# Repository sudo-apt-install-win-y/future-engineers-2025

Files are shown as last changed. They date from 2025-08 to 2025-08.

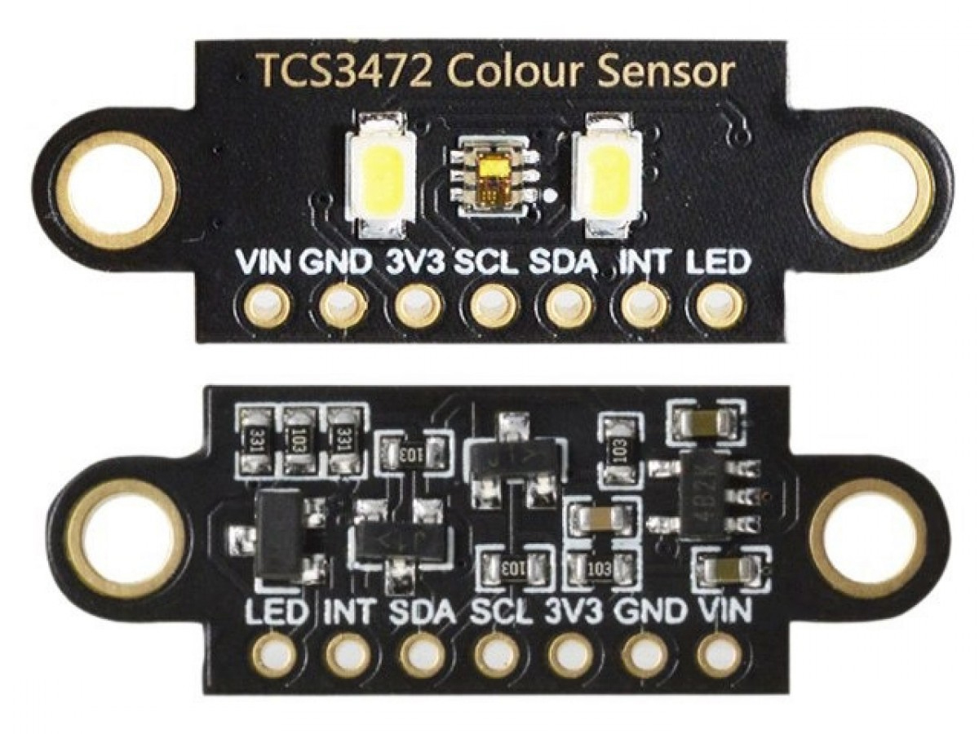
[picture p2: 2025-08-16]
docs/images/component_photos/TCS34725.jpg

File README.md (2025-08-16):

# sudo apt install win -y - WRO 2025 Future Engineers
**Category:** Future Engineers - Self-Driving Cars

**Team:** DJ_Theron, TheGuyInTheRedSuit

**Coach:** Jarret Williams

**Country:** South Africa

## Table of contents
### [Mobility Management](/docs/mobility-manegement.md)
### [Power and Sense Management](/docs/power-and-sense.md)
### [Obstacle Management](/docs/obstacle-management.md)
### [Pictures](/docs/images/)
### [Performance Videos](/videos/demo-vids.md)
### [3D Models](/hardware/3d_models/)
### [Source Code](/software/src/)
### [How to build the robot](/hardware/howtobuild.md)
### [How to setup the robot to run code](/software/setup.md)
### [BOM (Bill Of Materials)](/hardware/bom/bill-of-materials.csv)
### [Schematics](/hardware/schematics/)

---

## Hardware Overview
At the heart of our robot is a central processor that runs all operations, a [Raspberry Pi 4B 2GB](/docs/images/component_photos/RaspberryPi4B.jpg). Our robot features a Rear wheel drive and front wheel steering system (Ackermann), enabling easy turning and motion. Rubber tires are utilised for the grip they provide. The chassis's RWD function, explained earlier, is powered by a single 12V DC brushed motor. Steering functionality is provided by a 12V servo motor connected. 
( _An in depth mobility manegement document can be found [here](/docs/mobility-manegement.md)_ )
The robot uses four time-of-flight sensors ([VL53l0x](/docs/images/component_photos/vl53l0x.jpg)), one colour sensor ([tcs34725](/docs/images/component_photos/TCS34725.jpg)), one gyroscope and one Raspberry Pi Camera v3 to achieve sensor fusion and computer vision. The Pi is powered by a Waveshare UPS HAT B, which contains 2 18650 batteries. 3 18650 Batteries power the motors. Everything connects to a central ground. ( _An in-depth power and sensing document can be found [here](/docs/power-and-sense.md)_ )

## Software Architecture
We used Python to code our robot. The code consists of 3 main modules. round1.py handles the entirety of the Open Challenge (what we call Round 1). round1.py utilises the data gathered from the distance sensors, and it then uses a PID controller to keep itself between the walls of the course. round1.py also uses the colour sensor to detect the lines on the ground, which tell the robot when to turn. round2.py handles the entirety of the Obstacle Challenge (we call it Round 2). By using OpenCV contour and colour detection on live images captured from the camera, we can distinguish where and what colour the block in front of the robot is, and so the robot will steer the appropriate way around it. The code also checks for a purple item in the background, indicating a purple block. After seeing the purple block three times, it proceeds to parallel park between the purple blocks. button_watcher.py handles starting and stopping the programs and indicating what is happening using an led. It is run as a systemd service and it starts when the Pi powers on and listens for button presses. When the button is pressed after powering on it goes into "armed" mode which allows for a singular press to start the round1.py program and a long press to start the round2.py program. Once in a program the button can be pressed to stop the running program in case something goes wrong. All of our code is in Python (except the installer script which is written in bash). We used OpenCV for computer vision and a custom PID controller for sensor fusion.

## Hardware-Software Integration
There are 8 sensors on the robot we use to determine the 2 outputs that the robot has. There are 6 i2c sensor of which 4 are the Time of Flights, 1 is the colour sensor and the other is the  Gyroscipe. The time of flights connects to the raspberry pi using i2c adresses and provides distance data to round1.py. The colour sensor connects to the raspberry pi using i2c and provides RGB values to both round1.py and round2.py. The time of flights have xshut pins (connected to each their own GPIO) which are used to assign different i2c adresses to each and since the colour sensor doesnt have one we had to design one ourselves, using a transistor, also connected to a GPIO pin. The Gyroscope connects to the Raspberry Pi via i2c and provides yaw angle data to round1.py.

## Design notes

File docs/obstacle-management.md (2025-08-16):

# Round 1 Obstacles Management

In order to make our way around the track 3 times there were a few obstacles to overcome

## Knowing when to take a corner

Our robot looks at the lines on the ground and takes note of the colour. The line will be blue when we need to turn right and orange when we need to turn left. Once it detects the lines it will run a hardcoded cornering script to allow it to take the corner perfectly. l

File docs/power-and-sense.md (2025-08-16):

## Power and Sense Management
### Power
We use 3 18650 batteries to provide 10.8 - 11.1 volts to our motor driver board. The motor driver board powers our DC Motor and Servo. To power our Raspberry Pi 4 B we have 2 more 18650 Batteries in a Waveshare UPS Hat B. This provides a stable power source to our Pi at 7.2 - 7.4 volts directly onto the Pi's power rails through Pogo Pins.

### Time of Flight Sensors
Our robot has 4 VL53L0X Time of Flight sensors situated with 2 on either side of our robot to give us the distances between the walls and our robot. Using these, we also determine a rough angle of our robot by looking at the distances at the front and the back of our robot.

Instead of these Time of Flights, we would have preferred a lidar to detect the walls, maybe next year.

### Camera
The robot is also equipped with a Raspberry Pi Camera 3 Regular Angle (76 degrees) to see the red and green obstacles in round 2. 

### Direction Sensing
Our robot has a Gyroscope and accelerometer sensor (MPU60-50). We do not use the Accelerometer; we just use the Gyroscope to determine the angle of the robot. 

### Color sensing
Finally, we have a colour sensor to detect the orange and blue lines on the mat to know when to take the corner.

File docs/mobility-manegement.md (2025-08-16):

## Mobility Management
### Drivetrain type
Our robot is built like a normal RWD (Rear Wheel Drive) car you find in everyday life. This means it has two wheels at the rear of the robot, which provide drive. At the front of the robot, two wheels provide steering functionality. 
### Rear Drive Assembly
The rear axle is powered by a single 12V DC motor with external gears, which speeds the robot up to allow for faster driving around the board. These gears connect to a simple but reliable rear axle, which is held in place by two ball bearings on either side of the robot. These connect to two thick and grippy rubber wheels that provide strong traction to the board mat.
### Front Drive Assembly
The front wheels are not powered to provide traction but are used for steering to navigate obstacles, turn corners, and parallel park the robot. We used a standard 12V 180-degree servo motor to turn a certain amount or continue straight. The steering rack utilises Ackermann steering geometry to make sure that turns are taken properly, accounting for wheels on the inside and outside of a turn needing to trace out circles of different radii (since the inner wheel takes a tighter path while the outer wheel takes a wider path).

Ackermann Steering

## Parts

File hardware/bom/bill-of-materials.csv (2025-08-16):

Component | Description | Qty | Manufacturer | Purpose | Team_Fabricated | Source
Raspberry Pi 4B | Main computer 2GB RAM | 1 | RPi Foundation | Processing and vision | No | pishop.co.za
Pi Camera v3 | 8MP camera module | 1 | RPi Foundation | Track and object detection | No | pishop.co.za
DC Motor | 12V motor | 1 | Generic | Drive system | No | Hobby shop
Servo Motor | 180° standard servo | 1 | Generic | Steering control | No | Hobby shop
ToF Sensors | HC-SR04 distance sensors | 4 | Generic | Obstacle detection | No | Online supplier
Robot Chassis | Main frame structure | 1 | Custom | Mechanical support | No | Laser cut acrylic
Camera Mount | Camera holder | 1 | Custom | Vision system mount | Yes | 3D printed
Motor Driver | L298N dual H-bridge | 1 | Generic | Motor control | No | Electronics store
Custom PCB | Power distribution board | 1 | Custom | Wiring organization | Yes | Team designed
Battery | 7.4V Li-Po 1500mAh | 1 | Generic | Power supply | No | RC hobby store
Wheels | Rubber wheels 65mm | 4 | Generic | Movement and steering | No | Various suppliers
Hardware | Screws nuts spacers | Set | Generic | Assembly | No | Hardware store
Wiring | Jumper wires connectors | Set | Generic | Connections | No | Electronics store

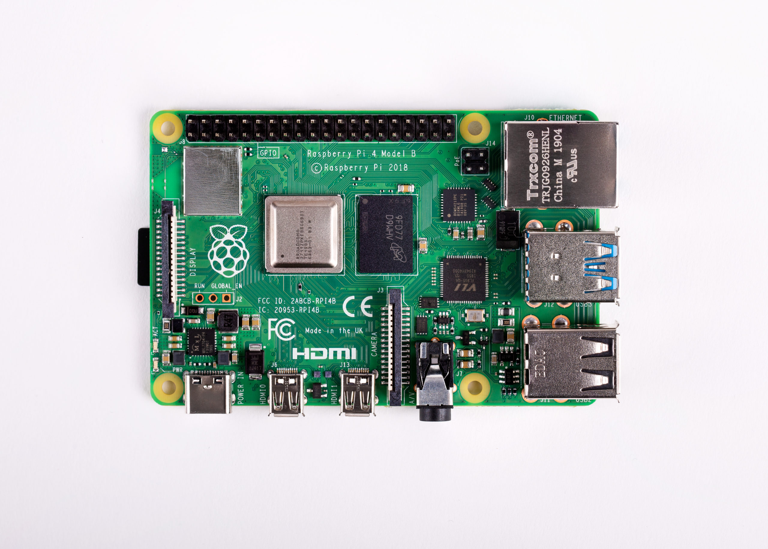
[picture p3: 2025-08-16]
docs/images/component_photos/RaspberryPi4B.jpg

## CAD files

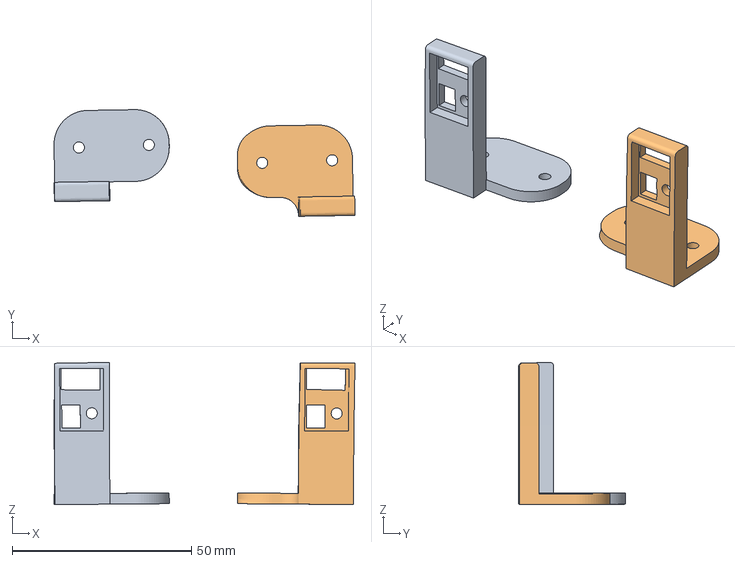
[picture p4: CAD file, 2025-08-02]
hardware/3d_models/ToF_Mount_Both.3mf
83.9 x 29.7 x 39.6 mm
ToFNicerLooking_Right.stl
ToFNicerLooking_Left.stl

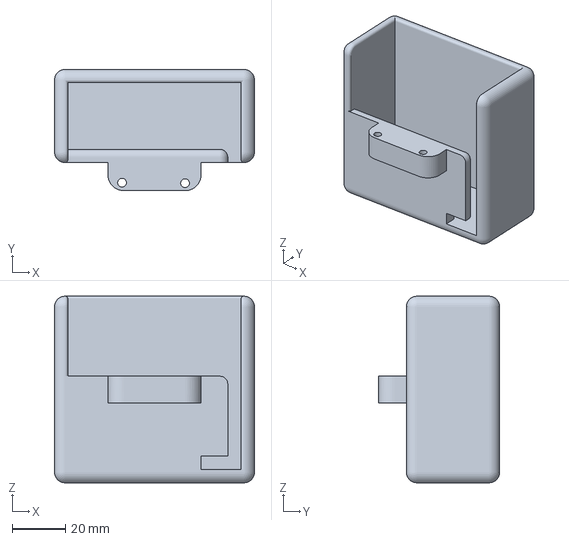
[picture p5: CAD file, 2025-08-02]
hardware/3d_models/Battery_Holder.3mf
75.0 x 45.5 x 70.0 mm

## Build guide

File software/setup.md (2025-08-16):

# How to setup the robot for code
Firstly you need to complete building the robot [here](/hardware/howtobuild.md)
## 1. Flash the SD Card
To get started you will need to flash the micro SD card that will be inserted into the Raspberry Pi
First go to [the raspberry pi downloads page](https://www.raspberrypi.com/software/) and download raspberry pi imager for your OS.
Then install the imager.
Open it. Insert the micro SD Card into your computer. Choose your model of pi on the app. choose full desktop environment. choose the microsd card. click flash. 

## 2. Setup the Pi
plug the microsd into your pi. turn it on. set up the pi by following the onscreen instructions. access the pi's terminal using ssh or a monitor and keybaord.

## 2. Run setup.sh
First you need to get the setup.sh code from its public github.
<pre>curl https://github.com/sudo-apt-install-win-y/setup-script/blob/main/setup.sh</pre>
Now you need to just run the bash file and everything should install.
<pre>bash setup.sh</pre>

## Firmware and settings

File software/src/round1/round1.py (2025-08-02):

import RPi.GPIO as GPIO
import time
import board
import busio
import digitalio
import adafruit_vl53l0x
import adafruit_tcs34725

IN1 = 17
IN2 = 27
ENA = 18
servo = 12

csensor = 0

Kp = 9
Ki = 0
Kd = 4

error = 0
current_time = 0
integral = 1
last_time = time.time()
dt = 0
steering_angle = 90
output = 0
last_error = 1

sensor1 = None
sensor2 = None
sensor3 = None
sensor4 = None

distance1 = 0
distance2 = 0
distance3 = 0
distance4 = 0

sensor_addresses = [0x30, 0x31, 0x32, 0x33]
sensor_shutdown_pins = [board.D5, board.D6, board.D13, board.D26]
sensors = []

turningright = False
turningleft = False


GPIO.setwarnings(False)
GPIO.setmode(GPIO.BCM)
GPIO.setup(IN1, GPIO.OUT)
GPIO.setup(IN2, GPIO.OUT)
GPIO.setup(ENA, GPIO.OUT)
GPIO.setup(servo, GPIO.OUT)

pwm2 = GPIO.PWM(ENA, 100)
pwm = GPIO.PWM(servo, 50)
pwm2.start(0)
pwm.start(0)

def forward(speed=100):
    """Rotate motor forward."""
    GPIO.output(IN1, GPIO.HIGH)
    GPIO.output(IN2, GPIO.LOW)
    pwm2.ChangeDutyCycle(speed)

def reverse(speed=100):
    """Rotate motor backward."""
    GPIO.output(IN1, GPIO.LOW)
    GPIO.output(IN2, GPIO.HIGH)
    pwm2.ChangeDutyCycle(speed)

def stop():
    """Stop the motor."""
    GPIO.output(IN1, GPIO.HIGH)
    GPIO.output(IN2, GPIO.HIGH)
    pwm.ChangeDutyCycle(0)

def coast():
    GPIO.output(IN1, GPIO.LOW)
    GPIO.output(IN2, GPIO.LOW)
    pwm.ChangeDutyCycle(0)

def set_angle(angle):
    duty = 2 + (angle / 18)
    GPIO.output(servo, True)
    pwm.ChangeDutyCycle(duty)
    time.sleep(0.5)
    GPIO.output(servo, False)
    pwm.ChangeDutyCycle(0)

def setupsensors():
    global sensors
    print("Setting up 4 sensors...")
    
    i2c = busio.I2C(board.SCL, board.SDA)
    
    # Create and shutdown all sensors
    xshuts = []
    for pin in sensor_shutdown_pins:
        x = digitalio.DigitalInOut(pin)
        x.direction = digitalio.Direction.OUTPUT
        x.value = False
        xshuts.append(x)

    time.sleep(0.1)

    for i, xshut in enumerate(xshuts):
        xshut.value = True
        time.sleep(0.1)
    
        sensor = adafruit_vl53l0x.VL53L0X(i2c)
        sensor.set_address(sensor_addresses[i])
        time.sleep(0.1) 
    
        # Reconnect all sensors using new addresses
    sensors = [
        adafruit_vl53l0x.VL53L0X(i2c, address=addr)
        for addr in sensor_addresses
    ]
    print("All sensors ready.")

    # Set up I2C communication
    i2c = busio.I2C(board.SCL, board.SDA)

    # Initialize the TCS34725 color sensor
    sensor = adafruit_tcs34725.TCS34725(i2c)

    # Optional: turn on built-in LED if available
    sensor.enable_led = True  # Turn off if your sensor has no LED or external lighting

def get_distance(index):
    if 0 <= index < len(sensors):
        return sensors[index].range
    return -1  # Error value

def setup():
    setupsensors()
    set_angle(90)

def get_distances():
    global distance1, distance2, distance3, distance4
    distance1 = get_distance(0)
    distance2 = get_distance(1)
    distance3 = get_distance(2)
    distance4 = get_distance(3)
    distance1 = distance1 / 10
    distance2 = distance2 / 10
    distance3 = distance3 / 10
    distance4 = distance4 / 10

def pidleft():
    get_distances()
    global distance1, distance2, distance3, distance4
    global last_time, last_error, current_time, error, integral
    global integral

    current_time = time.time()
    dt = current_time - last_time

    error = distance1 - distance2
    integral += error * dt
    derivative = (error - last_error) / dt

    output = Kp * error + Ki * integral + Kd * derivative

    steering_angle = 90 + output
    steering_angle = max(40, min(120, steering_angle))

    set_angle(steering_angle)

    last_error = error
    last_time = current_time

def pidright():
    get_distances()
    global distance1, distance2, distance3, distance4
    global last_time, last_error, current_time, error, integral

    current_time = time.time()
    dt = current_time - last_time

    error = distance3 - distance4
    integral += error * dt
    derivative = (error - last_error) / dt

    output = Kp * error + Ki * integral + Kd * derivative

    steering_angle = 90 + output
    steering_angle = max(40, min(120, steering_angle))

    set_angle(steering_angle)

    last_error = error
    last_time = current_time

def in_range(rgb, r_min, r_max):
    return all(low <= val <= high for val, low, high in zip(rgb, r_min, r_max))

setup()
forward(20)
while True:
    while True:
        r, g, b = csensor.color_rgb_bytes
        pidleft()

        if in_range((r, g, b), (100, 50, 30), (150, 80, 60)): #put the Blue codes
            print('cornering left')
            turningleft = True
            forward(30)
            time.sleep(0.2)
            set_angle(60)
            time.sleep(1)
            set_angle(90)
            forward(20)
            break

        elif in_range((r, g, b), (100, 50, 30), (150, 80, 60)): #put the orange codes
            print('cornering right')
            turningright = True
            forward(30)
            time.sleep(0.2)
            set_angle(120)
            time.sleep(1)
            set_angle(90)
            forward(20)
            break

        time.sleep(0.05)

    if turningleft == True:
        while True:
            r, g, b = csensor.color_rgb_bytes
            pidleft()
            if in_range((r, g, b), (100, 50, 30), (150, 80, 60)): #put the Blue codes
                print('cornering left')
                forward(30)
                time.sleep(0.2)
                set_angle(60)
                time.sleep(1)
                set_angle(90)
                forward(20)
                break
                
            time.sleep(0.05)
        
    elif turningright == True:
        while True:
            r, g, b = csensor.color_rgb_bytes
            pidright()
            if in_range((r, g, b), (100, 50, 30), (150, 80, 60)): #put the orange codes
                print('cornering right')
                turningright = True
                forward(30)
                time.sleep(0.2)
                set_angle(120)
                time.sleep(1)
                set_angle(90)
                forward(20)
                break
            
            time.sleep(0.05)

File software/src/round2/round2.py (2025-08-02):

import cv2
import numpy as np
import RPi.GPIO as GPIO
import time
import board
import busio
import digitalio
from picamera2 import Picamera2
import adafruit_tcs34725

# Set up I2C communication
i2c = busio.I2C(board.SCL, board.SDA)

# Initialize the TCS34725 color sensor
sensor = adafruit_tcs34725.TCS34725(i2c)

IN1 = 17
IN2 = 27
ENA = 18
servo = 12


GPIO.setwarnings(False)
GPIO.setmode(GPIO.BCM)
GPIO.setup(IN1, GPIO.OUT)
GPIO.setup(IN2, GPIO.OUT)
GPIO.setup(ENA, GPIO.OUT)
GPIO.setup(servo, GPIO.OUT)

pwm2 = GPIO.PWM(ENA, 100)
pwm = GPIO.PWM(servo, 50)
pwm2.start(0)
pwm.start(0)

def forward(speed=100):
    """Rotate motor forward."""
    GPIO.output(IN1, GPIO.HIGH)
    GPIO.output(IN2, GPIO.LOW)
    pwm2.ChangeDutyCycle(speed)

def reverse(speed=100):
    """Rotate motor backward."""
    GPIO.output(IN1, GPIO.LOW)
    GPIO.output(IN2, GPIO.HIGH)
    pwm2.ChangeDutyCycle(speed)

def stop():
    """Stop the motor."""
    GPIO.output(IN1, GPIO.HIGH)
    GPIO.output(IN2, GPIO.HIGH)
    pwm.ChangeDutyCycle(0)

def coast():
    GPIO.output(IN1, GPIO.LOW)
    GPIO.output(IN2, GPIO.LOW)
    pwm.ChangeDutyCycle(0)

def set_angle(angle):
    duty = 2 + (angle / 18)
    GPIO.output(servo, True)
    pwm.ChangeDutyCycle(duty)
    time.sleep(0.5)
    GPIO.output(servo, False)
    pwm.ChangeDutyCycle(0)

def read_colour():
    """Read color from the TCS34725 sensor."""
    r, g, b = sensor.color_rgb_bytes
    return r, g, b

# Initialize the camera
picam2 = Picamera2()
# Configure the camera
preview_config = picam2.create_preview_configuration()
picam2.configure(preview_config)
# Start the camera
picam2.start()

while True:
    lap_count = 0
    last_corner = None
    # Main loop
    while lap_count < 3:
        # Capture frame
        frame = picam2.capture_array()

    # Convert to HSV for color filtering
    hsv = cv2.cvtColor(frame, cv2.COLOR_RGB2HSV)
    # Define green color range in HSV
    lower_green = np.array([40, 70, 70])
    upper_green = np.array([80, 255, 255])
    # Define red color ranges in HSV (adjusted for lower light)
    lower_red1 = np.array([0, 70, 50])    # Lower saturation and value thresholds
    upper_red1 = np.array([10, 255, 255])
    lower_red2 = np.array([170, 70, 50])  # Lower saturation and value thresholds
    upper_red2 = np.array([180, 255, 255])
    
    # Create masks for green, red, and purple objects
    mask_green = cv2.inRange(hsv, lower_green, upper_green)
    mask_red1 = cv2.inRange(hsv, lower_red1, upper_red1)
    mask_red2 = cv2.inRange(hsv, lower_red2, upper_red2)
    mask_red = cv2.bitwise_or(mask_red1, mask_red2)

    # Combine masks for all objects
    mask_all = cv2.bitwise_or(mask_green, mask_red)
    # Apply Gaussian blur to reduce noise
    blurred = cv2.GaussianBlur(mask_all, (7, 7), 0)
    # Apply morphological operations to clean up the mask
    kernel = np.ones((5, 5), np.uint8)
    morph = cv2.morphologyEx(blurred, cv2.MORPH_CLOSE, kernel)
    # Use morph as binary image for contours
    thresh = morph
    # Find contours
    contours, _ = cv2.findContours(thresh, cv2.RETR_EXTERNAL, cv2.CHAIN_APPROX_SIMPLE)

    
    
    if contours:
        # Find the largest contour
        largest = max(contours, key=cv2.contourArea)
        area = cv2.contourArea(largest)
        M = cv2.moments(largest)
        if M["m00"] != 0:
            cx = int(M["m10"] / M["m00"])
            cy = int(M["m01"] / M["m00"])
            # Draw the center
            cv2.circle(frame, (cx, cy), 5, (0, 255, 0), -1)

            # Determine position
            width = frame.shape[1]
            if cx < width // 3:
                position = "Left"
            elif cx < 2 * width // 3:
                position = "Center"
            else:
                position = "Right"

            # Determine color of the tracked object (red or green only)
            color = "Unknown"
            if mask_green[cy, cx] > 0:
                color = "Green"
            elif mask_red[cy, cx] > 0:
                color = "Red"

            cv2.putText(frame, f"{color} {position}", (cx, cy-10), cv2.FONT_HERSHEY_SIMPLEX, 0.7, (255,0,0), 2)

            forward(30)
            if color == "Red" and position == "Right":
                set_angle(120)
            if color == "Red" and position == "Center":
                set_angle(100)
            if color == "Red" and position == "Left":
                set_angle(90)
            if color == "Green" and position == "Right":
                set_angle(90)
            if color == "Green" and position == "Center":
                set_angle(80)
            if color == "Green" and position == "Left":
                set_angle(60)

            # Use color sensor for cornering
            r, g, b = read_colour()
            # Simple blue/orange detection (tune thresholds as needed)
            if b > r and b > g and b > 100:  # Blue detected
                if last_corner != 'blue':
                    lap_count += 1
                    print(f'Lap {lap_count}: cornering left (blue detected)')
                    last_corner = 'blue'
                forward(30)
                time.sleep(0.2)
                set_angle(60)
                time.sleep(1)
                set_angle(90)
                forward(20)
            elif r > g and r > b and r > 100 and g > 50 and b < 50:  # Orange detected (tune as needed)
                if last_corner != 'orange':
                    lap_count += 1
                    print(f'Lap {lap_count}: cornering right (orange detected)')
                    last_corner = 'orange'
                forward(30)
                time.sleep(0.2)
                set_angle(120)
                time.sleep(1)
                set_angle(90)
                forward(20)

            # Print all relevant data
            print(f"Object color: {color}, position: {position}, center: ({cx}, {cy}), area: {area}, Sensor RGB: ({r}, {g}, {b})")
        # Flip the frame upside down and side to side for display
        flipped_display = cv2.flip(frame, -1)
        cv2.imshow("Frame", cv2.cvtColor(flipped_display, cv2.COLOR_RGB2BGR))
        if cv2.waitKey(1) & 0xFF == ord('q'):
            break

    # Clean up
    picam2.stop()
    cv2.destroyAllWindows()
    GPIO.cleanup()

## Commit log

2025-08-01 Add autonomous vehicle control script
    Introduces round1.py, a script for controlling a vehicle using four VL53L0X distance sensors and a PID algorithm for steering. Includes motor and servo control, sensor setup, and logic for cornering 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
2025-08-01 Add empty round2.py module
    Created a new round2.py file in the src/round2 directory. The file is currently empty and serves as a placeholder for future implementation.
2025-08-01 Add button watcher with LED feedback
    Introduces a Python script to monitor a GPIO button and provide LED feedback for short and long presses. Short presses flash the LED and launch one script, while long presses keep the LED solid and launch a different script.
    [button_watcher.py]
2025-08-02 added 3mfs/CAD files
    [Battery_Holder.3mf, ToF_Mount_Both.3mf]
2025-08-02 Integrate TCS34725 color sensor for cornering logic
    Added initialization and usage of the TCS34725 color sensor to detect color codes for left and right cornering. Replaced turn counter logic with color-based detection, refactored cornering conditions, and updated control flow to use RGB values for navigation decisions.
    [round1.py]
2025-08-02 Add color-based object tracking and motor control
    Implements object detection using camera and TCS34725 color sensor to control motor and servo based on detected color and position. Includes HSV color filtering, contour detection, and logic for lap 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
2025-08-11 Update README.md
    add motor specification
2025-08-11 Update README.md
    add front wheel drive journaling
2025-08-11 Update README.md
    added explanation for ackermans steering
2025-08-16 Moved 3d files to correct place
    [Battery_Holder.3mf, ToF_Mount_Both.3mf]
2025-08-16 added csv bom template and edited some values
    [bill-of-materials.csv]
2025-08-16 Update power-and-sense.md; Update setup.md
2025-08-16 Created setup.sh; updated readme.md; Created button-watcher service; updated power and sense.md
2025-08-16 im tired
